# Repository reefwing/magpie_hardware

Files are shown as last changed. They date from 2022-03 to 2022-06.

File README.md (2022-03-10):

# Magpie Drone DS3 Construction
 PCB Design and BOM for the Magpie Drone.

 ## Overview

 The Nexgen team is designing their own drone to be used for school incursion courses with a duration of 1–3 days. The drone will be controlled by an Arduino Nano 33 BLE or an Arduino Portenta H7 (i.e. the Mbed OS based Arduino cores).

There is some additional hardware and interfacing requirements which we have spoken about in [part 2 of our article on Writing your own Flight Controller Software](https://reefwing.medium.com/how-to-write-your-own-flight-controller-software-part-2-bc7f27214bb2). Our Power Distribution Board (PDB), makes it easy to include these in our drone build. 

Note that there are two different PDB’s for the Nano 33 BLE and the Portenta H7 because they use different header configurations (Portenta uses the MKR form factor and the Nano uses the Nano form factor). This repository describes the construction of the Nano 33 BLE version.

The Power Distribution Board includes the following:

- The provision of a regulated 5VDC from the LiPo battery. The auxillary connectors are connected to this 5V bus when the left two pins of the 5V AUX header is bridged.
- Driving circuitry for the on-board passive piezo buzzer.
- Inverting and level shifting SBUS interface for the X8R remote control transceiver.
- Power indication (LED’s) for battery and 5V.
- Voltage divider to measure the battery voltage.
- Nano 33 BLE external reset.
- Interface points for the X8R SBUS, RSSI and Telemetry, LiPo (XT-60), and ESC power and control.

## Construction

Check the Printed Circuit Board for any obvious defects, then check that you have all the parts you need before firing up the soldering iron.

Start by soldering the low profile components, resistors, transistors, LED’s, JST-SH 2 pin connectors (AUX 5VDC) and piezo buzzer. If the resisitors get mixed up, use a multimeter to make sure that you are mounting the right component. All the part values are screen printed on the PCB. The correct transistor orientation is marked on the PCB.

Double check that you have the correct model voltage regulator. You should be able to read on the part LM1084–5V. The LM1084-ADJ part wont work in this circuit design and we received these when we ordered the 5V model. It took a while to work out what the problem was as the parts look identical.

Mount the regulator and capacitors next. It is easier to do this before the Nano stackable headers are in place. As the Nano sits on top of these components, the regulator needs to be mounted flat (use an M3 nut and bolt to secure it in place before soldering) and the capacitors need to be pushed all the way in (or laid flat). There should be just enough room, but check this before soldering the capacitors.

The correct orientation for the LM1084 is with the heatsink hard against the mounting hole. The heatsink should be touching the PCB. The tantalum capacitors are also polarised. Normally the positive pins are marked and these should match up with the “+” marked pin on the PCB.

We used 0.1' Header Pins in lieu of switches for the 5V AUX and RESET. If you want the 5V bus available you need to bridge the left 2 pins on the 5V AUX. You will need 5V for the X8R remote control transceiver as a minimum so you could just use a wire bridge on those two pins instead of using 0.1' Header Pins. If you do use the header pins, I placed some sticky tape over the top to hold them in place. Solder just one pin and then you can adjust if the part isn’t straight.

Finally, mount the Nano stackable headers. The easiest way to keep these in the correct location is to place them in the PCB and mount the Nano 33 BLE. Then solder one pin on each side and double check that everything looks ok. You can then solder the rest of the pins. The Nano header pins are relatively far apart (compared to the Portenta H7 at least), but it is always better to use less solder and add more if required.

Congratulations! You have completed construction of the Magpie Drone Power Distribution board.

## Testing

Remove the Nano 33 BLE if you have it in place. Connect up the LiPo that you plan to use with your drone. For our prototype we were using a 1300 mAh, 2S (nominal 7.4V), battery. The size of the battery that you use is constrained by two things:

- The Nano 33 BLE: which can handle 5–21V input (Vin); and
- The LM1084–5: 6.5–25V input.

Consequently, our minimum operating voltage is 6.5V and our maximum is 21V.
An individual LiPo cell has a nominal voltage of 3.7V but when fully charged can be around 4.3V although it will quickly drop to 3.7V under normal use. When depleted, the cell will be around 3V.

From this we can determine that the range of suitable LiPo battery serial configurations is 2S (i.e. 2 x 3.7 = 7.4) to 4S (4 x 4.3 = 17.2V).

Once you have connected the battery, you should see the following:

- The green VBAT LED on;
- The orange 5V AUX LED on (if you have bridged the two left most 5V AUX pins), otherwise this LED will be off;
- You should be able to measure 5V on the test pins in the top left corner (again assuming AUX is bridged); and
- You should measure the battery voltage on the P1 and P2 test pins at the bottom centre of the board.

If you don’t see any of the above, immediately disconnect your battery and check for errors. If the above checks are ok you can disconnect your battery and then plug in the Nano 33 BLE. When you reconnect the battery your Nano should power up as normal. Make sure you plug the board in the right way round. The USB port should be towards the bottom of your board.

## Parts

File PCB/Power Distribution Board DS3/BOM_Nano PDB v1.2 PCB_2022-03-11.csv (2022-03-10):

ID | Name | Designator | Footprint | Quantity | Manufacturer Part | Manufacturer | Supplier | Supplier Part | Price
1 | XT60PW-M | CN1 | XT60PW-M PCBLIB | 1
2 | 1N4002 | D1 | DO-41 | 1
3 | SWITCH-SPDTKIT | S2,S1 | SWITCH-SPDT_KIT | 2
4 | 1K 0.25W | R5,R8,R7 | RTH025W | 3
5 | 10K 0.25W | R6,R4 | RTH025W | 2
6 | PS1440P02BT | BUZZER1 | BUZ-TH_BD14.0-P5.00-D0.7-FD | 1
7 | JST-SH 6-Pin Male | JP3 | 1X06-1.25MM_JST | 1
8 | GND | P4 | ONE_O | 1
9 | +5 VDC | P3 | ONE_O | 1
10 | TRANSISTOR_NPN2N3904 | Q1 | TO-92 | 1
11 | JST XH | CN3,CN2 | JST-PH-2-THM | 2
12 | BC32740TA | Q2 | 2N3906TA | 1
13 | 10uF | C2,C1 | CAP-TAN-S2.5 | 2
14 | 2 Pin Header | U3 | 2 PIN MOLEX | 1
15 | LM1084-5V | IC1 | SEEED-TO-220 | 1
16 | 150R 0.25W | R2 | RTH025W | 1
17 | 270R 0.25W | R1 | RTH025W | 1
18 | 18K 0.25W | R3 | RTH025W | 1
19 | XT60 | U1 | XT60 THROUGH HOLE | 1
20 | 3 PIN SC | U6,U5 | XH2.54_3PIN | 2
21 | LED-3MM | LED2,LED1 | LED-3MM/2.54 | 2
22 | ARDUINO_NANO_33 | U2 | ARDUINO_NANO_33_IOT | 1

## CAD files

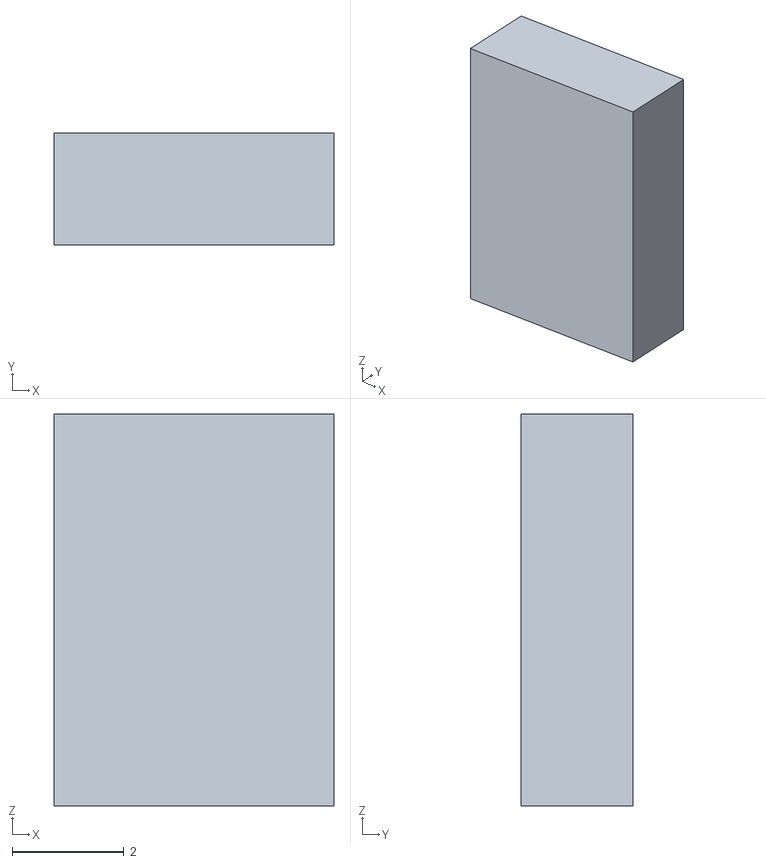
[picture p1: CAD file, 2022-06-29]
STL Files/X8RAntennaBlock_v3.stl
5.00 x 2.00 x 7.00

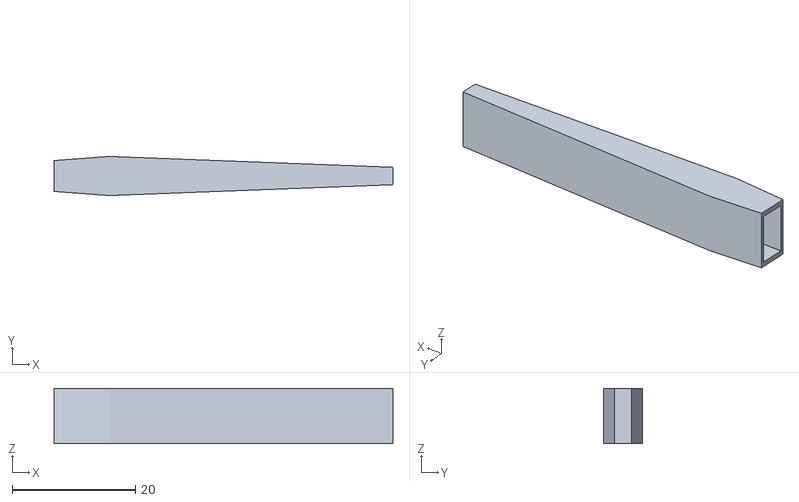
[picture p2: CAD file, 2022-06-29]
STL Files/X8RAntenna_v3.stl
55.0 x 6.35 x 9.00

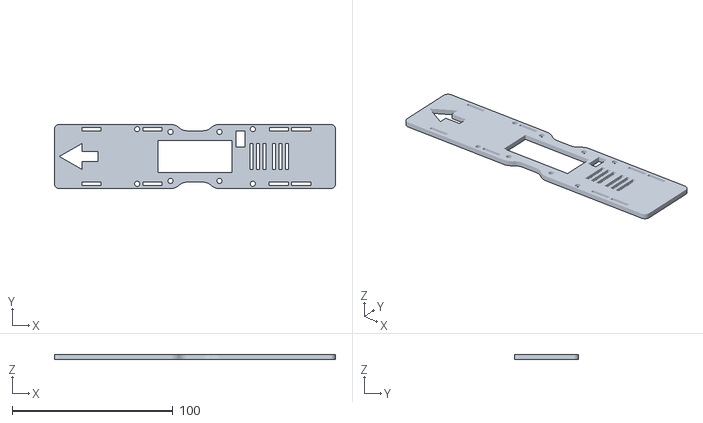
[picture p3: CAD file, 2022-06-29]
STL Files/TopDeck_v3.stl
175.0 x 40.1 x 3.00

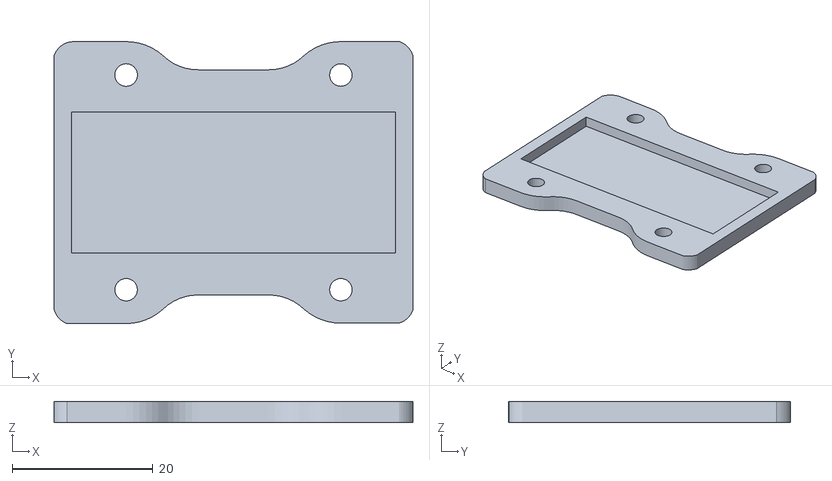
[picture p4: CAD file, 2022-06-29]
STL Files/SunRoof_v3.stl
51.0 x 40.1 x 3.00

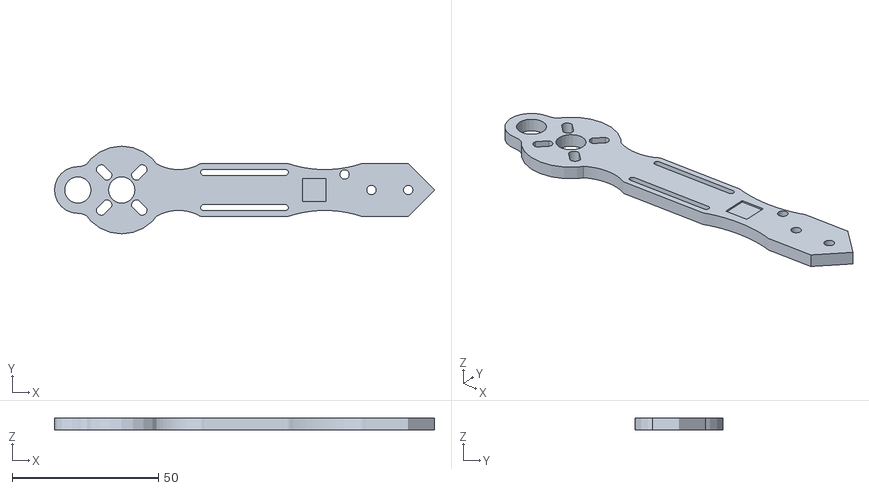
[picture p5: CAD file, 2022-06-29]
STL Files/ArmLeft_v3.stl
130.0 x 30.0 x 4.00

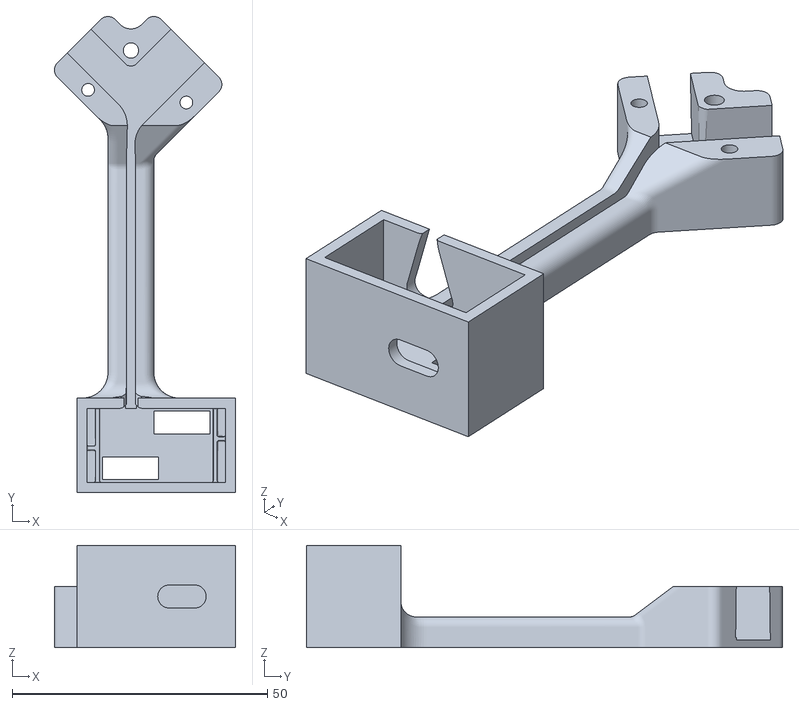
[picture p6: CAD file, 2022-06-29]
STL Files/X8RMount_v3.stl
35.5 x 93.2 x 20.0

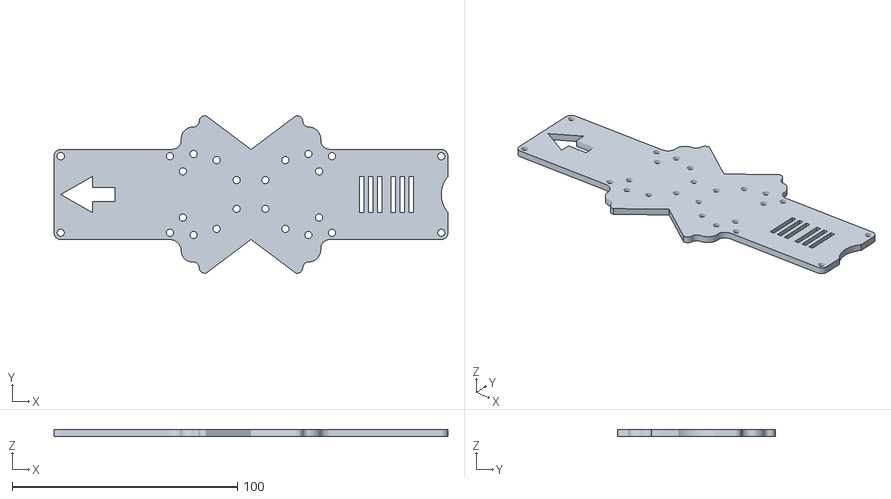
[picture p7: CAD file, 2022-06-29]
STL Files/BottomDeck_v4.stl
175.0 x 70.0 x 3.00

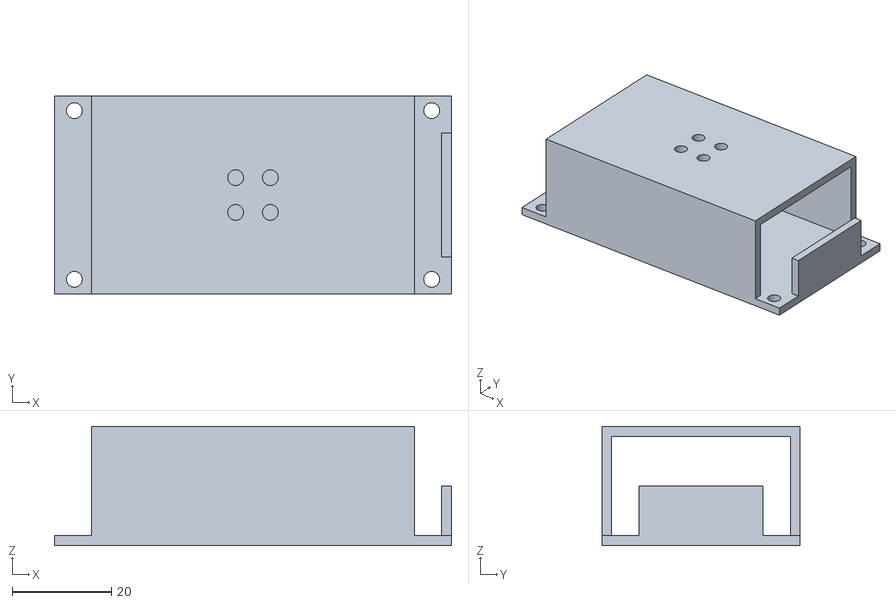
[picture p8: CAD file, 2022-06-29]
STL Files/BatteryMount_v2.stl
80.0 x 40.0 x 24.0

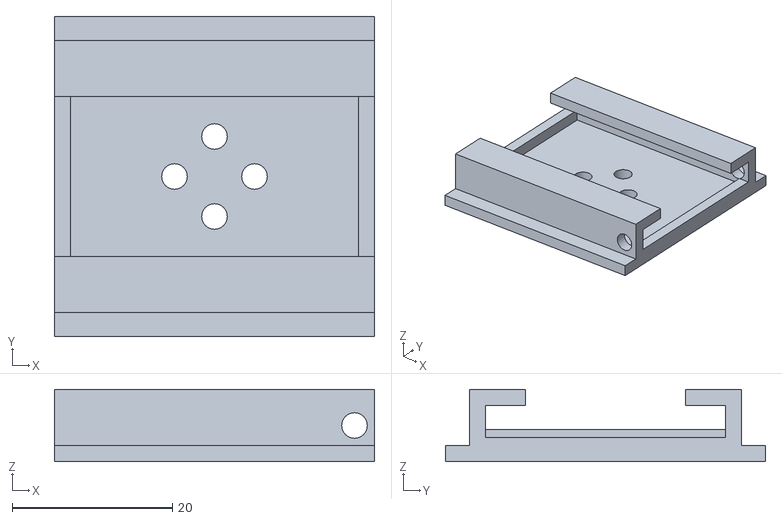
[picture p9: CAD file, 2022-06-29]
STL Files/DroneClipA_v2.stl
40.0 x 40.0 x 9.00

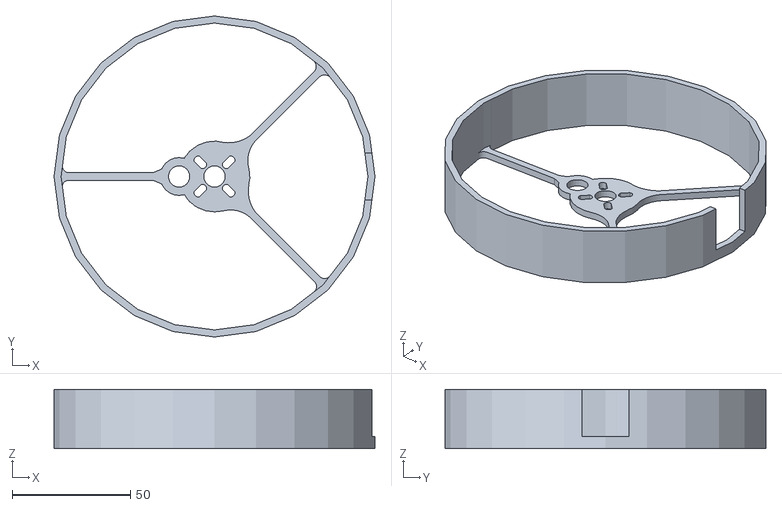
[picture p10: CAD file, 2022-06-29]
STL Files/PropGuard_v3.stl
136.0 x 136.0 x 25.0

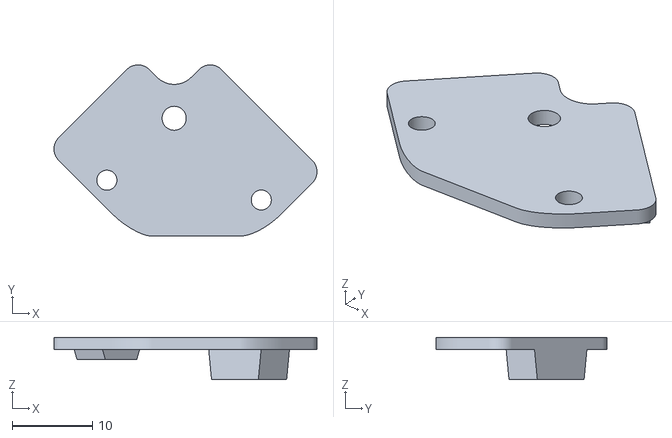
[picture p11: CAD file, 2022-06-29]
STL Files/X8RCover_v3.stl
32.8 x 21.3 x 5.25

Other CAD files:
STL Files/ArmRight_v3.stl

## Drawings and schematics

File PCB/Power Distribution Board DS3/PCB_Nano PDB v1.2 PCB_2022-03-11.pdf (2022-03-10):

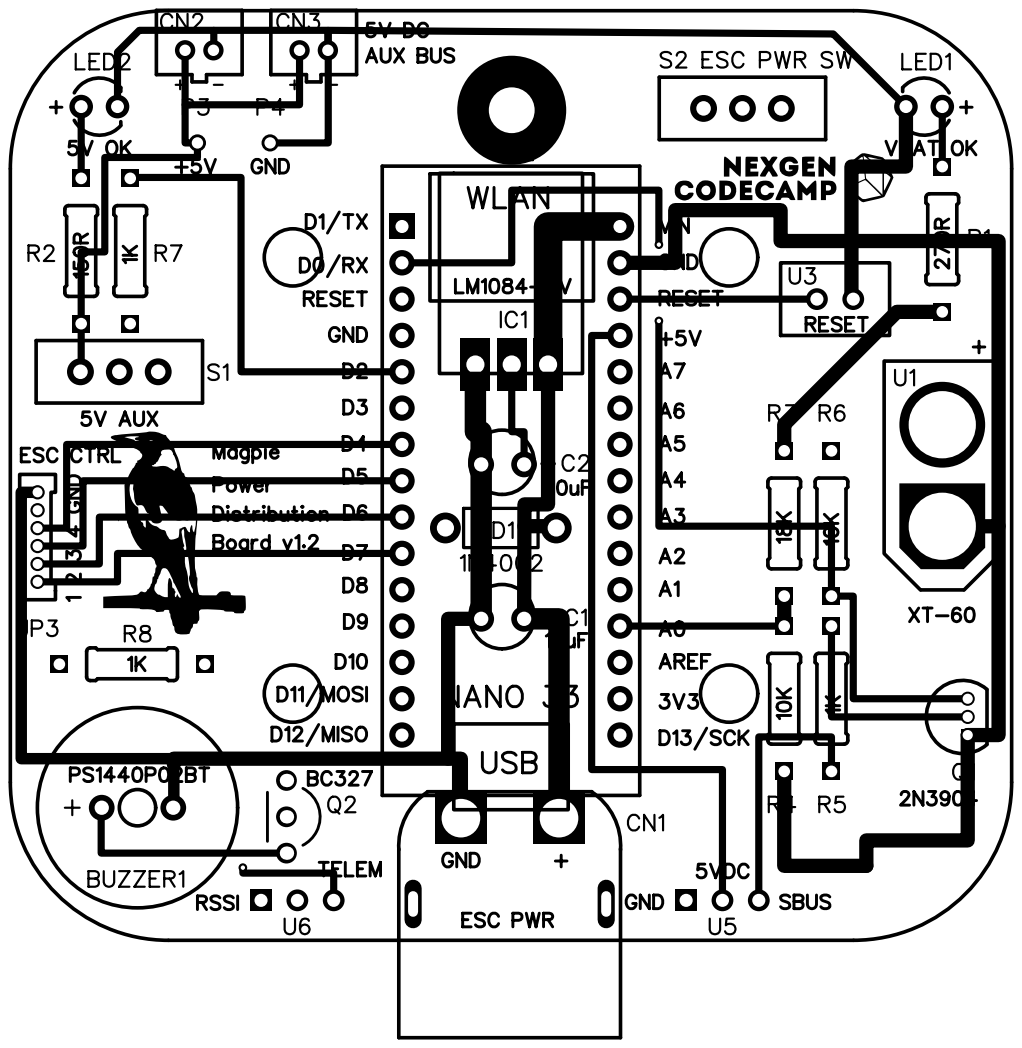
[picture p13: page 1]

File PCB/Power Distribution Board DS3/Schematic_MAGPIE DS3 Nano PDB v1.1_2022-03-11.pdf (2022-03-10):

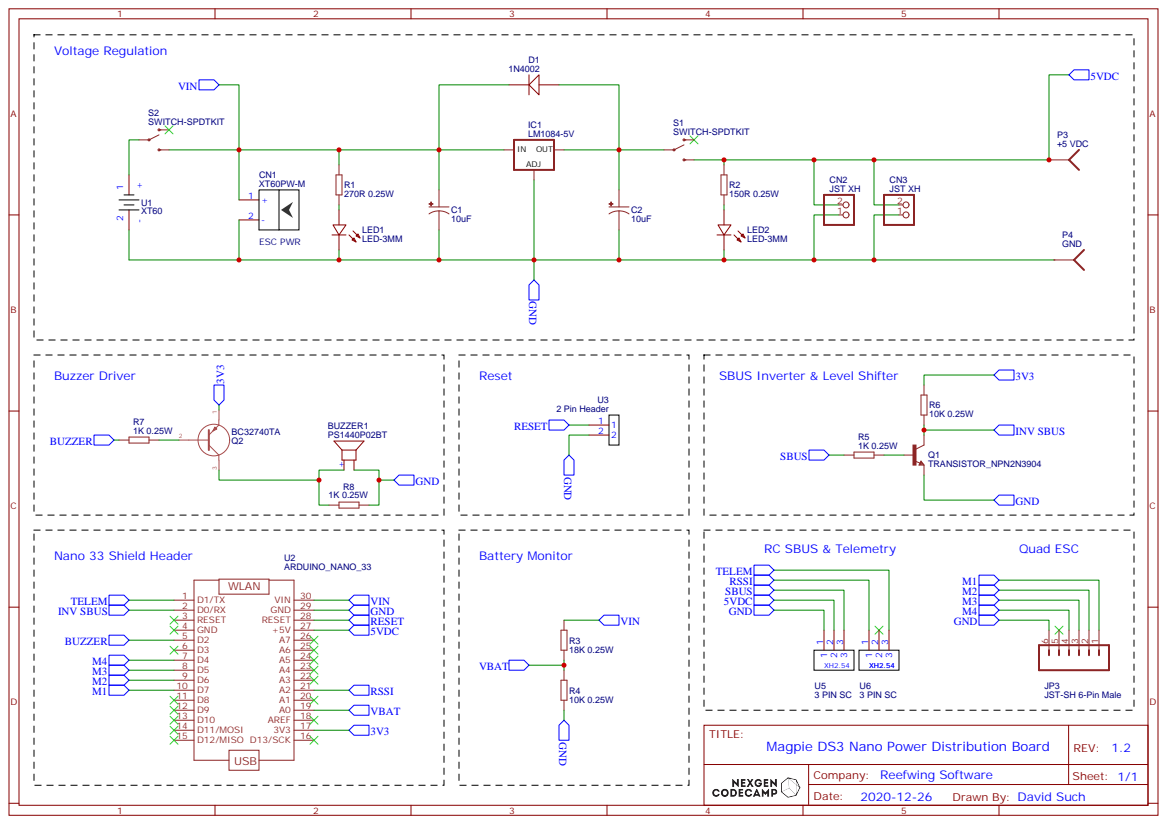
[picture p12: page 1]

SBUS Inverter & Level Shifter

JST-SH 6-Pin Male

Drawn By: David Such
